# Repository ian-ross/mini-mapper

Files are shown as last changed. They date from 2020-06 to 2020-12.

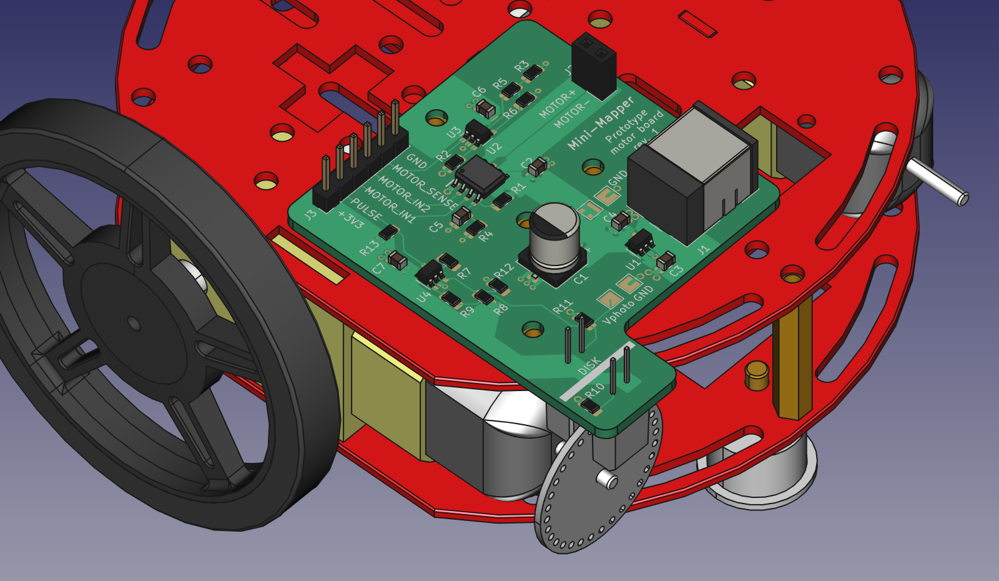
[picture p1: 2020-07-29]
prototypes/motor-board/doc/motor-prototype-setup/motor-prototype-setup.png

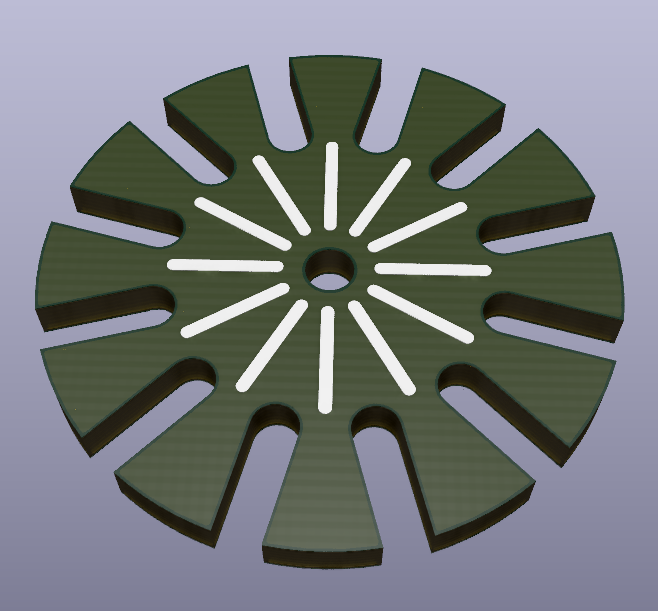
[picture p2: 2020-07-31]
prototypes/motor-board/motor-encoder-disk/v2/motor-encoder-disk.png

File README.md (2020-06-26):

# Mapping robot project experiment

Goals:

 - Learn some electronics
 - Write some interesting embedded software
 - Experiment with developing teaching materials

## Tools

 - KiCad 5.1.6

## Notes

 - All KiCad projects need to include path to top-level `lib`
   directory as a project-specific library path. This should be set up
   as a path relative to `${KIPRJMOD}`.

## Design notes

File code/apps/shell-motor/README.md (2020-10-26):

# PWM shell application

Sets up 5 kHz PWM timers on:

 * TIM10: PB8
 * TIM3: PA6, PA7, PC8, PC9

## Commands

pwm1 {on|off}
pwm4 {on|off}

## Variables

pwm1-state
pwm1-polarity
pwm1-duty
pwm1-reload

pwm4-state
pwm4-polarity-1
pwm4-polarity-2
pwm4-polarity-3
pwm4-polarity-4
pwm4-duty-1
pwm4-duty-2
pwm4-duty-3
pwm4-duty-4
pwm4-reload

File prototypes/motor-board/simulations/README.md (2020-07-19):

# Motor encoder circuit simulations

These simulations are intended to explore the threshold and hysteresis
setup for the comparator used with the photointerrupter for the motor
encoder disk.

The comparator used in the simulations is the LT1017, though that's
not what's used in the real circuit.

## Simulations

There are four different simulations here:

 * `phototransistor-saturation.asc` just demonstrates how
   phototransistors go into saturation when drive sufficiently hard,
   using a photoisolator out of the LTSpice libraries for
   experimentation.

 * `no-noise/no-noise.asc` uses a simulated current signal without any
   superimposed noise to look at how the comparator works in a simple
   case.

 * `with-noise/jitter.asc` uses a simulated current signal with some
   superimposed noise, showing the bad effects of noise leading to
   spurious comparator output transitions when the phototransistor
   current crosses the comparator threshold slowly. This is no good
   for counting pulses, so we need to add hysteresis.

 * `with-noise/hysteresis.asc` uses the same simulated current signal
   withh superimposed noise, but includes a small amount of hysteresis
   in the comparator circuit, which eliminates the spurious
   transitions in the comparator output and gives a clean pulse train
   suitable for counting the motor encoder disk holes passing the
   optical aperture of the photointerrupter.

## Phototransistor current simulations

The `scripts/gen-signal.py` script generates simulated current signals
from the phototransistor in the photointerrupter as the motor encoder
disk turns. See the `../doc/photoencoder-signal` directory for the
details of how these simulations work.

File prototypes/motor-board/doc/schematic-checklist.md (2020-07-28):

# Schematic review checklist

Is the design passively or actively safe? For example, if an MCU or
FPGA is being programmed, held in reset, or in their POR, does the
circuit enter a safe / idle / known state? Is the circuit only “hot”
under control (can it be)?

Can all relevant environmental changes be detected? If changes in
environment indicate a change in operating state or mode, can they be
detected? Examples: VBUS high on a self-powered USB device, SD card in
socket, a particular connector plugged in, water ingress, etc.

BOM has full orderable part numbers including all options and sufixes.
BOM is complete including PCB, enclosure, screws, bags, accessories,
memory cards, manuals, customer boxes, labels, master shipping carton.

## General

* [X] CAD ERC 100% clean. If some errors are invalid due to toolchain
      quirks, each exception must be inspected and signed off as invalid.
* [X] Verify pin numbers of all schematic symbols against datasheet or
      external interface specification document (if not yet board proven).
* [X] Schematic symbol matches chosen component package
* [X] Thermal pads are connected to correct power rail (may not always
      be ground)
* [?] Pull-up / -down resistors appropriate value for expected
      environment/noise?
* [X] Enable pins checked for polarity. Not all datasheets indicate
      this well, pin description text checked? Part number verified
      for ICs with orderable polarity configurations?
* [X] Enable and shutdown pins pulled to the correct level when not
      under control? (e.g. shut down unless controlled)
* [X] Pull-ups on open-drain, open-collector nets? Values for required
      slew rates / throughput / noise?
* [X] Passive / buffered visual indicators (e.g. LEDs) at appropriate
      level for the idle level of the protocol? (e.g. UART idle high,
      SPI clock idle low, etc)
* [X] Exposed pads on no-leads packages tied to correct net? Needs to
      be left floating?

## Passive components

* [X] Power/voltage/tolerance ratings specified as required
* [X] Ceramic capacitors appropriately de-rated for C/V curve
* [X] Polarized components specified in schematic if using electrolytic caps etc

## Power supply

### System power input

* [X] Check total input capacitance and add inrush limiter if needed

### Regulators

* [X] Verify estimated power usage per rail against regulator rating
* [X] Linear regulators and voltage reference ICs are stable with selected output cap ESR

### Decoupling

* [X] Decoupling present for all ICs
* [X] Decoupling meets/exceeds vendor recommendations if specified
* [X] Bulk decoupling present at PSU

### General

* [X] All power inputs fed by correct voltage
* [X] Check high-power discrete semiconductors and passives to confirm
      they can handle expected load
* [X] Analog rails filtered/isolated from digital circuitry as needed

## Signals

### Digital

* [X] Signals are correct logic level for input pin
* [X] Pullups on all open-drain outputs
* [X] Active high/low enable signal polarity correct

### Analog

* [X] Verify polarity of op-amp feedback

### Debugging / reworkability

* [X] Use 0-ohm resistors vs direct hard-wiring for strap pins when
      possible
* [X] Provide multiple ground clips/points for scope probes
* [X] Dedicated ground in close proximity to analog test points
* [X] Test points on all power rails
* [X] Test points on interesting signals which may need probing for
      bringup/debug

## Thermal

* [X] Power estimates for all large / high power ICs
* [X] Thermal calculations for all large / high power ICs
* [X] Specify heatsinks as needed

## Power

* [X] Power pins tied to correct voltage rail?
* [X] Dropout voltage of regulators checked against complete
      range/tolerance of source supply? Not just nominal/ideal rating.
* [X] Minimum load met for stability of all regulators?
* [X] Final circuit maximum load rechecked against regulator ratings?
* [X] Digital ICs have correct number and value of bypass capacitors
      for frequencies in use?
* [X] Bypass and output capacitor values checked for all regulators?
      Correctly derated? Appropriate  ESR for stability?
* [X] Analog rails properly decoupled with ferrites / inductors /
      capacitors?

## Sensors / Signal Conditioning

* [X] Dividers and filters buffered with op-amp before ADC?
* [X] Op-amp stability checked given load capacitance on output?
* [X] Unused op-amps in dual or quad packages terminated?

## Connectors

* [X] Power and its ground on same connector?
* [X] Related inputs/outputs on same connector?

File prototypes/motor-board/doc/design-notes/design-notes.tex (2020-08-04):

\documentclass[a4paper,11pt,article]{memoir}

\usepackage[utf8]{inputenc}
\usepackage{fourier}
\usepackage{amsmath,amssymb}
\usepackage{xstring,ifthen,xcolor}
\usepackage{xspace}
\usepackage{url}

\usepackage{color}
\definecolor{orange}{rgb}{0.75,0.5,0}
\definecolor{magenta}{rgb}{1,0,1}
\definecolor{cyan}{rgb}{0,1,1}
\definecolor{grey}{rgb}{0.25,0.25,0.25}
\newcommand{\outline}[1]{{\color{grey}{\scriptsize #1}}}
\newcommand{\todo}[1]{{\color{red}\textit{\textbf{#1}}}}
\newcommand{\note}[1]{{\color{blue}\textit{\textbf{#1}}}}
\newcommand{\citenote}[1]{{\color{orange}{[\textit{\textbf{#1}}]}}}

\usepackage{tikz}
\usepackage{pgfmath}
\usetikzlibrary{calc,shapes,positioning}

\title{Mini-Mapper:\,Motor prototype board design notes}
\author{Ian~Ross}

\graphicspath{{figs/}}

\begin{document}

\maketitle

These notes describe the motor prototype board for the Mini-Mapper
robot. This is intended as a platform to test motor driver and motor
encoder setup, and to develop motor early control algorithms
(particularly constant-speed PID control and soft start).

\section{Requirements}

\begin{itemize}
  \item{Power single Dagu DG01D gearmotor (4.5\,V, 250\,mA max.);}
  \item{PWM speed control, bidirectional, coast/brake functionality;}
  \item{Rotation measurement using optical encoder;}
  \item{Interface to STM32F767ZI Nucleo-144 board;}
  \item{Clean mechanical design for interface between motor and motor
    encoder disk.}
\end{itemize}

\section{Mechanical design}

\begin{itemize}
  \item{Final PCB to be mounted on top chassis plate of robot: do this
    also for prototype motor board, to get placement right.}
  \item{Principal constraints are:
    \begin{itemize}
      \item{Access to mounting holes on top chassis plate
        (there is interference with the motor under some holes);}
      \item{Clearance under PCB:\@{}both for the possibility of
        mounting components on the bottom of the PCB and for space for
        routing wires and to avoid shorts to chassis plate from THT
        components;}
      \item{Alignment of photoencoder with motor encoder disk:
        photointerrupter slot and optical axis need to align with the
        holes in the motor encoder disk, there needs to be no
        interference between the photointerrupter and the motor body,
        and there needs to be little enough interference between the
        photointerrupter and the top chassis plate to make modifying
        the chassis plate easy.}
  \end{itemize}}
  \item{Motor encoder disk needs to be manufacturable by hand, which
    means a simple disk with holes, rather than slots. This leads to a
    strong alignment requirement in the vertical direction between the
    motor encoder disk and the photointerrupter optical axis.}
\end{itemize}

\section{Component choices}

\paragraph{Motor driver: Toshiba TB67H450FNG}

Chosen to match supply voltage requirements for motors, to have a
standard PWM-capable control interface, internal current regulation
and an easy-to-use package.

\paragraph{Current sense opamp: TI TLV9051}

This is a low-side current sensing application, which imposes some
requirements on the input range of the opamp. The TLV9051 is
specifically intended for this application.

\paragraph{Photointerrupter: Vishay TCST1202}

Phototransistor type photointerrupter, because we're not going to get
a perfect transistion between full occlusion and full non-occlusion of
the photointerrupter's optical aperture, so it will be useful to be
able to set thresholds for occluded/non-occluded switching. The
primary constraints here are mechanical, since most devices like this
have similar electrical characteristics. The selected device has a
0.5\,mm wide optical aperture, which matches up with some simulations
I've done, and it can be mounted without interference with the motor
body using reasonably sized standard hardware (i.e. 5\,mm standoffs
between the PCB and the top chassis plate).

\paragraph{Motor encoder comparator: TI LMV331}

The requirements here are simple, so a jellybean comparator is a good
choice. Not an LM339 though! Something more modern. I chose a TI
LMV331, which is a single supply device available in an SOT-23 package.

\paragraph{4.5\,V regulator: TI TLV702}

Need a linear regulator to produce 4.5\,V from a 5\,V input: TI's
TLV702 is cheap, simple, can provide 300\,mA and comes in a 4.5\,V
version.

\paragraph{Power connectors}

Barrel jack from 5\,V power supply is 5.5\,mm OD with a 2\,mm pin. I
believe the positive connection is to the pin. We want to use the CUI
PJ-063AH, for which there is a footprint in the KiCad libraries.

\paragraph{Motor connectors}

2-hole 0.1'' header vertical socket (motor leads have individual 0.1''
pins).

\paragraph{Nucleo board connectors}

6-hole 0.1'' header vertical header (two digital motor control inputs,
one analogue motor coil current sense output, one digital encoder
pulse output, 3.3\,V supply, ground). I have leads with a pin on one
end and a socket on the other, so putting headers on the motor board
will allow these leads to connect from there to the sockets on the
Nucleo board.

\section{Schematic capture}

\subsection{Motor driver}

\begin{itemize}
  \item{Power decoupling: following schematic in application note.}
  \item{Current sense resistor: motors run from a 4.5\,V supply, and
    want to keep the maximum sense voltage to some small fraction of
    this. For a maximum current of 250\,mA, a sense resistor of
    400\,$\mathrm{m\Omega}$ gives a maximum sense voltage of 100\,mV.}
  \item{Current regulation: the maximum allowed motor coil current is
    set following the datasheet's instructions for setting the
    $V_\mathrm{ref}$ input.}
  \item{Current sensing: this is a simple non-inverting amplifier
    setup converting the 0--100\,mV sense voltage to a suitable range
    for input to the microcontroller's ADC (0--3\,V). Following a
    suggestion in a TI app
    note\footnote{\url{http://www.ti.com/lit/an/slva959a/slva959a.pdf}}
    about layout for motor drivers, the current sensing connections
    are highlighted to be routed as a differential pair (trying the
    net tie trick suggested in the app note to make the routing less
    confusing).}
\end{itemize}

\subsection{Motor encoder}

\begin{itemize}
  \item{The LED side of this is simple: take $V_f$ and $I_f$ from the
    datasheet and find a suitable resistor based on the power rail
    (3.3\,V, taken from the Nucleo board).}
  \item{On the phototransistor side, a current sensing resistor is
    needed. The light current from the phototransistor is quoted as
    being at least 1\,mA, and typically 2\,mA, but remember that we'll
    only be getting about half of that because of the size of the
    holes in the motor encoder disk. A $5.7\,\mathrm{k\Omega}$
    resistor will give a sense voltage of 2.85\,V for a phototransistor
    current of 0.5\,mA. Higher phototransistor currents will just lead
    to the phototransistor saturating, so the sense voltage will also
    be close to the positive rail.}
  \item{The threshold to use for the comparator used to turn the
    analogue output from the phototransistor into pulses for counting
    holes in the encoder disk is set at $V_{\mathrm{cc}} / 2$. This is
    conservative enough to be higher than any likely ``dark current'',
    which includes the true dark current from the phototransistor plus
    any additional current due to ambient light falling on the
    phototransistor.}
  \item{A bare comparator will produce spurious output transistions in
    the presence of noise (see simulations), so some hysteresis is
    included. The resistor values selected give a hysteresis of about
    0.1\,V.}
\end{itemize}

\subsection{Nucleo board interface}

Connections:
\begin{itemize}
  \item{3.3\,V power and ground;}
  \item{Two GPIO outputs for motor control (PWM-capable);}
  \item{One ADC input for motor coil current sense;}
  \item{One GPIO input for photoencoder pulses (interrupt-capable).}
\end{itemize}

Use 0.1'' headers on motor board, and connect to Nucleo board using
jumper cables, since the connections we'll want are pretty spread out.

\begin{center}
  \begin{tabular}{lcccc}
    \textbf{Use} & \textbf{PCB} & \textbf{Nucleo} & \textbf{Conn} & \textbf{Pin} \\
    Power  & \texttt{3V3} & \texttt{+3V3} & CN8 & 7\\
    Ground & \texttt{GND} & \texttt{GND} & CN8 & 11 \\
    Motor control & \texttt{IN1} & \texttt{PD14} (\texttt{TIM4\_CH3}) & CN7 & 16 \\
    Motor control & \texttt{IN2} & \texttt{PD15} (\texttt{TIM4\_CH4}) & CN7 & 18 \\
    Motor current sense & \texttt{Vsense} & \texttt{PA3} (\texttt{ADC123\_IN3}) & CN9 & 1 \\
    Encoder pulses & \texttt{PULSE} & \texttt{PG3} & CN8 & 16 \\
  \end{tabular}
\end{center}

\todo{Label connections with use and Nucleo pin names on silkscreen.}

\subsection{Power}

Supplies:
\begin{itemize}
  \item{Need 4.5\,V (250\,mA max.) for motor, and 3.3\,V for logic.}
  \item{For prototype board, use 3.3\,V supply from Nucleo board, and
    use external 5\,V wall wart supply plus linear regulator for
    4.5\,V supply.}
\end{itemize}

\subsubsection{3.3\,V}

For the 3.3\,V supply, the current draw is approximately:

\begin{center}
  \begin{tabular}{lc}
    \textbf{Component} & \textbf{Worst case current draw (mA)} \\
    Motor driver (control inputs) & 0.11 \\
    TLV9051 opamp & 0.45 \\
    LMV331 comparator & 0.1 \\
    TCST1202 photointerrupter & $25 + 2$ \\
    \textbf{Total} & \textbf{28} \\
  \end{tabular}
\end{center}

This 28\,mA total is well within the 500\,mA limit for the 3.3\,V
supply from the Nucleo board, so we can run the 3.3\,V devices on the
motor prototype board directly from the 3.3\,V supply from the Nucleo board.

\subsubsection{4.5\,V}

The current draw for the 4.5\,V supply can be up to 250\,mA from the
motor, plus perhaps 5\,mA for the motor driver. This is too much for
the 5\,V supply from the Nucleo board to supply reliably, so we need
to use a separate power source for the 4.5\,V supply.

We will use a 5\,V wall wart power supply with a TI TLV702 LDO
regulator (which comes in a 4.5\,V version and can supply 300\,mA).

\section{Layout}

\todo{Mechanical board outline: photoencoder placement, mounting
  holes. Measure carefully directly from chassis plate: just motor
  axis, mounting holes and photointerrupter location.}

\section{Assembly}

\paragraph{Mounting hardware}

5\,mm spacers between PCB and top chassis plate, M2.5 bolts and nuts
to secure PCB.

\paragraph{Power supply connections}

\end{document}

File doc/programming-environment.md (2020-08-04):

# Programming environment

Keep this as simple as possible, and keep it fun (for me, that
means Emacs, rather than an IDE). Requirements:

 * Emacs integration
 * C++
 * GCC toolchain
 * Makefiles?
 * OpenOCD + GDB
 * Minimal libraries: more or less just CMSIS register definitions to
   start with; later possibly FreeRTOS as well.

## Toolchain

### Compiler

GCC (gcc-arm-none-eabi-9-2020-q2-update)

https://developer.arm.com/-/media/Files/downloads/gnu-rm/9-2020q2/gcc-arm-none-eabi-9-2020-q2-update-x86_64-linux.tar.bz2

(Use this instead of AUR package, because it includes GDB as well.)

Install in `/big/opt/gcc-arm-none-eabi-9-2020-q2-update` and add
`/big/opt/gcc-arm-none-eabi-9-2020-q2-update/bin` to `PATH`.

### Programmer

OpenOCD

(available as an Arch package)

### Debugger

GDB

## Platform/libraries

CMSIS

## Build system

CMake

## Editor assistance

All in Emacs!

### IDE features

All this comes from `cmake-ide` + `rtags`:

 - Indexing/references
 - Code completion
 - Syntax highlighting

Need to set up some keybindings for `rtags`.

### Compile/flash/debug

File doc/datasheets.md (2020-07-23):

# Motors

 - [Dagu DG01D](http://www.dagurobot.com/DG01D-L)

# Motor drivers

### Diodes Inc.

 - [ZXBM5210](https://www.diodes.com/assets/Datasheets/ZXBM5210.pdf)

### Rohm

 - [BD60203EFV](https://fscdn.rohm.com/en/products/databook/datasheet/ic/motor/dc/bd60203efv-e.pdf)

### ST Micro

 - [STSPIN250](https://www.st.com/resource/en/datasheet/stspin250.pdf)

### TI

 - [DRV8832](https://www.ti.com/lit/ds/symlink/drv8832.pdf)
 - [DRV8833C](https://www.ti.com/lit/ds/symlink/drv8833c.pdf)
 - [DRV8833](https://www.ti.com/lit/ds/symlink/drv8833.pdf)
 - [DRV8835](https://www.ti.com/lit/ds/symlink/drv8835.pdf)
 - [DRV8836](https://www.ti.com/lit/ds/symlink/drv8836.pdf)
 - [DRV8837C](https://www.ti.com/lit/ds/symlink/drv8837c.pdf)
 - [DRV8837](https://www.ti.com/lit/ds/symlink/drv8837.pdf)
 - [DRV8838](https://www.ti.com/lit/ds/symlink/drv8838.pdf)
 - [DRV8847](https://www.ti.com/lit/ds/symlink/drv8847.pdf)
 - [DRV8848](https://www.ti.com/lit/ds/symlink/drv8848.pdf)
 - [DRV8871](https://www.ti.com/lit/ds/symlink/drv8871.pdf)

### Toshiba

 - [TB6552FTG](https://toshiba.semicon-storage.com/info/docget.jsp?did=16151&prodName=TB6552FTG)
 - [TB6559FG](https://toshiba.semicon-storage.com/info/docget.jsp?did=10158&prodName=TB6559FG)
 - [TB6641FTG](https://toshiba.semicon-storage.com/info/docget.jsp?did=11265&prodName=TB6641FTG)
 - [TB67H301FTG](https://toshiba.semicon-storage.com/info/docget.jsp?did=14095&prodName=TB67H301FTG)
 - [TB67H450FNG](https://toshiba.semicon-storage.com/info/docget.jsp?did=65346&prodName=TB67H450FNG)
 - [TC78H600FTG](https://toshiba.semicon-storage.com/info/docget.jsp?did=13606&prodName=TC78H600FTG)
 - [TC78H651AFNG](https://toshiba.semicon-storage.com/info/docget.jsp?did=64622&prodName=TC78H651AFNG)
 - TC78H660FTG

Also, [Motor Solutions Catalog](https://toshiba.semicon-storage.com/info/docget.jsp?did=11639)

# Op-amps

- [TI TLV9051](https://www.ti.com/lit/ds/symlink/tlv9052.pdf)

# Photointerrupters

 - [Vishay TCST1202](https://www.vishay.com/docs/83764/tcst1103.pdf)

# Comparators

 - [TI LMV331](https://www.ti.com/lit/ds/symlink/lmv331.pdf)

# Linear regulators

 - [TI TLV702](https://www.ti.com/lit/ds/symlink/tlv702.pdf)

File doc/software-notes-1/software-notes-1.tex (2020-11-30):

\documentclass[a4paper,11pt]{article}

\usepackage[utf8]{inputenc}
\usepackage{fourier}
\usepackage{amsmath,amssymb}
\usepackage{xstring,ifthen,xcolor}
\usepackage{xspace}
\usepackage{url}

\usepackage{color}
\definecolor{orange}{rgb}{0.75,0.5,0}
\definecolor{magenta}{rgb}{1,0,1}
\definecolor{cyan}{rgb}{0,1,1}
\definecolor{grey}{rgb}{0.25,0.25,0.25}
\newcommand{\outline}[1]{{\color{grey}{\scriptsize #1}}}
\newcommand{\todo}[1]{{\color{red}\textit{\textbf{#1}}}}
\newcommand{\note}[1]{{\color{blue}\textit{\textbf{#1}}}}
\newcommand{\citenote}[1]{{\color{orange}{[\textit{\textbf{#1}}]}}}

\usepackage{tikz}
\usepackage{pgfmath}
\usetikzlibrary{calc,shapes,positioning}

\title{Mini-Mapper Software 1:\,Motor prototype board}
\author{Ian~Ross}

\graphicspath{{figs/}}

\begin{document}

\maketitle

These notes describe software development for the motor prototype
board for the Mini-Mapper robot. This is intended as a platform to
test motor driver and motor encoder setup, and to develop motor early
control algorithms (particularly constant-speed PID control and soft
start).

I'm intending to develop all the software for the Mini-Mapper as
``bare metal'' C++. Although I'll probably end up using an RTOS later
on (almost certainly FreeRTOS), I'm going to start with a simple event
loop without an RTOS. I'll use a Nucleo board with an STM32F767ZI
microcontroller on it for development experiments, and will choose a
suitable STM32 processor to put on the final Mini-Mapper boards based
on experiences using the Nucleo board. I'm not going to use any HAL
libraries from ST Micro because I'm interested in writing device
drivers myself.

The basic requirements I want to follow are:

\begin{itemize}
  \item{\textbf{Language} Firmware written in C++, maybe doing some
    experiments with Rust later on.}
  \item{\textbf{Libraries} Use only low-level CMSIS hardware
    definitions, writing my own C++ HAL.}
  \item{\textbf{Build system} Use Make for building, possibly adding
    Meson on top of this later on.}
  \item{\textbf{IDE} Use Emacs as an IDE, setting up the necessary
    tools for comfortable development.}
  \item{\textbf{Communications} Develop a command shell to run on the
    Nucleo board, talking to a PC over a USB serial port. This will
    make it easy both to do ad hoc experiments directly talking to the
    shell with Minicom, but also to write GUI front-ends for
    experiments and data collection using Python GTK or something
    similar. (This is the approach I used for my Teensy Load project,
    and I find it really useful.)}
  \item{\textbf{STM32 features} Clocks; power; USB serial (USART + DMA
    + interrupts); GPIOs and timers for PWM motor control; ADC for
    motor coil current sensing; GPIO input, interrupt and timer for
    motor encoder pulse detection.}
\end{itemize}

I want to cover the following topics in this prototyping phase:
\begin{enumerate}
  \item{Platform setup: clocks, power, etc.}
  \item{CMSIS familiarisation.}
  \item{Blinky: platform test, clock setup, GPIO setup.}
  \item{USART setup with interrupts for RX and DMA for TX.}
  \item{USB serial command shell.}
  \item{PWM demo: more GPIO setup, timer setup, USB serial control,
    view output using AD2.}
  \item{First pass experiment GUI: commanding of motor state (on/off,
    forward/backward, PWM duty cycle), monitoring of motor coil
    current and motor encoder pulses; data saving; real-time
    graphing.}
  \item{Encapsulation of motor abstractions: \texttt{Motor::Driver}
    for PWM driver, \texttt{Motor::Torque} for motor coil current
    measurement for torque estimation, \texttt{Motor::Encoder} for the
    encoder disk measuring motor rotation and
    \texttt{Motor::Controller} for the overall control of all motor
    functions.}
  \item{Constant speed PID control, including independent optical
    speed measurement.}
  \item{Soft start/ramp control.}
\end{enumerate}

This should be enough for the first ``direct control'' milestone.

\section{Initial setup}

\subsection{Platform and tools}

\begin{itemize}
  \item{I'm using the \texttt{arm-none-eabi} version of GCC, which is
    pretty standard.}
\end{itemize}

\subsection{CMSIS}

\begin{itemize}
  \item{The only files taken from the ST Micro-supplied code are the
    header files \texttt{stm32f767xx.h}, \texttt{stm32f7xx.h} and
    \texttt{core\_cm7.h} (and some compiler support files that they
    include), the startup file \texttt{startup\_stm32f767xx.s}, the
    linker script \texttt{STM32F767ZITx\_FLASH.ld}, and
    \texttt{system\_stm32f7xx.c}, which is a small file including a
    couple of support functions to help with clock setup.}
  \item{The header files provide register-level access to all the core
    functionality of the Cortex-M7 processor (\texttt{core\_cm7.h})
    and the peripherals provided on the STM32F767ZI
    (\texttt{stm32f767xx.h} and \texttt{stm32f7xx.h}).}
  \item{The \texttt{core\_cm7.h} also provides some basic functions
    for dealing with some core processor features, like cache control,
    the interrupt controller and the SysTick timer.}
  \item{I'm basically going to use anything in these files freely, and
    I'm happy to look at examples in the STM32 HAL code to work
    through any problems I have with my own HAL code, but I'm going to
    write more or less everything starting at the bare metal ``write
    to registers'' level, since this seems like the best way to get a
    good understanding of how things really work.}
\end{itemize}

\subsection{Blinky}

\section{Software architecture}

\section{USB serial shell}

\subsection{USART setup}

\subsection{Command shell}

\section{PWM demonstration}

\section{Experiment front-end GUI}

\section{Microcontroller setup}

The Nucleo board has an STM32F767ZI processor on it.

\subsection{Motor driver}

\begin{itemize}
  \item{The Toshiba motor driver has an application note where they
    seem to suggest using $f_{\mathrm{PWM}} = 30\,\mathrm{kHz}$.}
  \item{For a 10-bit resolution PWM duty cycle, this gives a clock
    frequency of $1024 \times 30\,\mathrm{kHz} = 30.72\,\mathrm{MHz}$.}
  \item{The clock input on Nucleo board is 8\,MHz by default. To use
    this, the STM32 should be set to run on the HSE clock (High-Speed
    External) with external bypass (\texttt{RCC\_CR:HSEBYP} = 1,
    \texttt{RCC\_CR:HSEON} = 1).}
  \item{The main clock PLL should be set up with
    \texttt{RCC\_PLLCFGR:PLLSRC} = 1 (HSE), \texttt{RCC\_PLLCFGR:PLLM}
    = 4 (VCO input: 2\,MHz), \texttt{RCC\_PLLCFGR:PLLN} = 128 (VCO
    output: 256\,MHz), \texttt{RCC\_PLLCFGR:PLLP} = 4 (PLL output:
    64\,MHz), and enabled with \texttt{RCC\_CR:PLLON} = 1.}
  \item{The APB prescalers need to be set to make the low-speed
    prescaler give a frequency of less than 45\,MHz:
    \texttt{RCC\_CFGR:PPRE1} = 4 (divide by 2 to give 32\,MHz).}
  \item{The system clock needs to be set to use the PLL:
    \texttt{RCC\_CFGR:SW} = 2.}
  \item{Using a 64\,MHz system clock and a 11-bit resolution PWM duty
    cycle yields a PWM frequency of 31.25\,kHz.}
\end{itemize}

\subsection{Motor torque measurement}

\subsection{Motor encoder}

The motor encoder uses a photointerrupter and an encoder disk on the
motor shaft. The motor shaft rotation rate is reduced by a 48:1
gearbox to drive the wheels.

Here are some basic questions and notes on the software approach for
capturing the edge transitions from the encoder.

\textit{How to do edge capture? Can you do capture on multiple pins
  using the same timer? Can you do both rising and falling edges at
  the same time?}

\begin{itemize}
  \item{Timers with input capture are basically all timers except TIM6
    and TIM7 basic timers.}
  \item{Timers with multiple input capture channels are TIM9, TIM12 (2
    channels); TIM2, TIM3, TIM4, TIM5 (4 channels); TIM1, TIM8 (4
    channels).}
  \item{Typical times we'll want to measure:
    \begin{itemize}
      \item{Wheel turning at 90 rpm (max, equivalent to 28.3 cm/s
        linear speed) => encoder turning at 90 x 48 = 4320 rpm = 72
        Hz.}
      \item{Disk has 12 teeth => tooth frequency = 72 x 12 = 864 Hz.}
      \item{If teeth/gaps are same size, edge freq. = 864 x 2 = 1728
        Hz. (Teeth and gaps aren't same size, but this is
        indicative.)}
      \item{So time between edges will be 578.7 μs.}
   \end{itemize}}
  \item{If we have a timer with a prescaler set to give a count
    frequency of 1 MHz, then a 16-bit counter will be able to measure
    times of up to 65.536 ms. A 32-bit counter will be able to measure
    times of up to 4294.97 s (i.e. 1 hr 11 min 34.97 s).}
  \item{At 1 mm/s linear speed, we see 1 / (60π) * 48 * 12 * 2 = 6.11
    edges per second, i.e. an inter-edge time of 163.6 ms. Seems like
    a 32-bit timer might be easier in this case...}
  \item{If we use a 32-bit timer, we can also reduce the prescaler to
    get a higher count frequency and corresponding better timing
    accuracy.}
  \item{The 32-bit timers are TIM2 and TIM5, both of which have four
    capture channels.}
  \item{GPIO inputs for capture channels have to be assigned as
    specific alternate functions. There seem to be enough redundant
    assignments to make this easy enough to do.}
  \item{Can either get an interrupt on the capture event, or get the
    capture timer count transferred via DMA and get an interrupt on
    DMA transfer complete. (For our purposes, an interrupt on each
    capture event is probably simplest to deal with, because we need
    to look at the GPIO level to know whether we have a rising or
    falling edge. In the ISR for the capture, we can check the GPIO
    level, bundle that up with the capture count and the channel we're
    looking at, and emit an event carrying all that information for
    later processing.)}
  \item{Capture edge polarity is controlled by the CCxP and CCxNP
    fields in the TIMx->CCER register: setting both of these bits
    captures both rising and falling edges.}
\end{itemize}

\textit{What information do we want to make available? Ultimately we
  want to provide a speed measurement, possibly with different kinds
  of smoothing (none: latest instantaneous value, boxcar smoothing
  over sample time, exponentially weighted smoothing?), but we also
  probably want access to raw time values as well, i.e. times of the
  last N edge transitions.}

\begin{itemize}
  \item{For a single encoder, we expect to get a sequence of
    alternating rising and falling edges. We'll store the edge type
    (rising or falling) and the timer count when the edge occurred.
    We'll keep the last N edge times, retiring eges when they get too
    old or we need to reuse storage space.}
  \item{We want to be able to retrieve time differences between edges
    and to convert them into rotation rates and linear speeds, both on
    an instantaneous basis and smoothed over the collected data (for
    the last 500 ms or something similar?).}
  \item{To start with, let's provide functions to retrieve time
    differences between adjacent edges (i.e. of opposite polarity) and
    between adjacent edges of the same polarity.}
\end{itemize}

\textit{What sort of time resolution do we need? And what to do about
  the really slow cases when the wheel is more or less stopped? Do we
  need some sort of rollover counter to time longer periods?}

\begin{itemize}
  \item{A single edge corresponds to 60π / 48 / 12 / 2 = 0.16 mm
    (assuming symmetry of rising and falling edges).}
  \item{Using a 32-bit timer running at 1 MHz, we can get 1 μs
    resolution for each edge. At maximum speed (90 rpm for the wheel,
    i.e. 60π * 1.5 = 282.74 mm/s), 1 μs corresponds to a linear
    distance of 0.28 μm. At lower speeds, the linear distance
    resolution is correspondingly finer.}
  \item{As noted above, with a timer count frequency of 1 MHz, a
    32-bit counter is able to measure times of up to 4294.97 s (i.e. 1
    hr 11 min 34.97 s).}
  \item{Both of these factors indicate that a 1 MHz 32-bit timer is
    pretty huge overkill... So let's go with that then!}
\end{itemize}

\end{document}

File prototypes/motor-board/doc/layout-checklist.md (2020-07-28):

# Layout review checklist

## General

* [X] [Schematic review](schematic-checklist.md) complete and signed
      off, including pin swaps done during layout
* [X] DRC set up to fab constraints before layout starts?
* [X] Layout DRC 100% clean
* [X] Double check the drill vs annular ring size for vias?
* [X] Passives have Traces coming into pads symmetrically? Traces
      comming into opposing “sides” of pads can cause solder
      migration, tombstoning, or stresses when the board cools.
* [X] Margin to edge of board checked? Appropriate given board
      break-away (V-score or mouse bites)? Mouse bites can easily
      pull/crack solder mask at 20 mil in.
* [X] Components can be reworked without removing others?
* [X] Thermal reliefs for all pads of serviceable components?

## Decoupling

* [X] Decoupling caps as close to power pins as possible
* [X] Low inductance mounting used for decoupling (prefer ViP if
      available, otherwise "[]8" shaped side vias

## DFM / yield enhancement

* [X] All design rules within manufacturer's capability
* [X] Minimize use of vias/traces that push fab limits

## Footprints

* [X] Confirm components are available in the selected package
* [X] Confirm components (especially connectors and power regulators)
      are capable of desired current in the selected package
* [X] Verify schematic symbol matches the selected package
* [X] Confirm pinout diagram is from top vs bottom of package
* [X] (recommended) PCB printed 1:1 on paper and checked against
      physical parts
* [X] 3D models obtained (if available) and checked against footprints
* [X] Soldermask apertures on all SMT lands and PTH pads

## Power

* [X] Traces have sufficient width for current and allowable
      temperature rise?
* [X] Sufficient trace spacing for voltage?
* [X] Highest ground currents closest to supply return?
* [X] Via size and count appropriate for current?
* [X] Thermal vias for thermal pads?
* [X] Tenting set appropriately for thermal vias?
* [X] Thermal reliefs disabled for power component pads?
* [X] Separate supply rail traces to multiple regulators?

## Connectors

* [X] Drivers near connectors they are driving signals on?

## Mechanical

* [X] Confirm all connectors to other systems comply with the
      appropriate mechanical standard (connector orientation, key
      position, etc)
* [X] LEDs, buttons, and other UI elements on outward-facing side of
      board
* [X] Clearance around pluggable connectors for mating cable/connector
* [X] Clearance around mounting holes for screws
* [X] Confirm PCB dimensions and mounting hole size/placement against
      enclosure or card rack design
* [X] Verify mounting hole connection/isolation
* [X] Components not physically overlapping/colliding
* [X] Clearance provided around solder-in test points for probe tips
* [X] Drill holes checked? Correct hole spacing to mounting hardware?
* [X] Drill hole plating checked?
* [X] Adequate clearance around mounting holes for both the mounting
      hardware and the tool that fastens it?

## Thermal

* [X] Thermal reliefs used for plane connections (unless via is used
      for heatsinking)
* [X] Solid connections used to planes if heatsinking
* [X] Ensure thermal balance on SMT chip components to minimize risk
      of tombstoning

## Solder mask

* [X] Confirm SMD vs NSMD pad geometry
* [X] Adequate clearance around pads (typ. 50 um)
* [X] Soldermask relief set appropriately given expected soldermask
      expansion?
* [X] Soldermask minimum spoke size met?
* [X] Soldermask relief around fiducials?
* [X] Soldermask removed for all pads?

## Silkscreen

* [X] Text size within fab limits
* [X] Text not overlapping drills or component pads
* [X] Text removed entirely in, or moved outside of, high component/via density areas
* [X] Traceability markings (rev, date, name, etc) provided
* [X] Text mirrored properly on bottom layer
* [X] Test points labeled if space permits
* [X] Check fab silkscreen DPI? Can legend be printed clearly?
* [X] Pin-1 indicator visible after component is placed on board?
* [X] Power pins labeled with polarity and voltage ranges?
* [X] Connector pinouts printed on both sides of board and mirrored?
      (if two-sided silkscreen)
* [X] Part number, revision number, date code present?
* [X] Legend references all facing one or two directions?

## CAM production

* [X] KiCAD specific: rerun DRC and zone fills before exporting CAM
      files to ensure proper results
* [X] Export gerber/drill files at the same time to ensure consistency
* [X] Visually verify final CAM files to ensure no obvious
      misalignments

## Programming and Test

* [X] Test points on all important clock and data pins?
* [X] More test points?
* [X] Sure, but maybe more test points?
* [X] Ground reference test points near all high speed signals that
      might need to be probed?

## Sensing

* [X] Analog sensors close to their ADC or buffered soon?
* [X] ADCs on or toward digital part of layout? (ADCs use fast
      oscillators)
* [X] Feedback dividers accidentally bypassed with capacitor
      placement?

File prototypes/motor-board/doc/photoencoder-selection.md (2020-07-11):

# Photoencoder selection

## Type

 - Two options: phototransistor or "photo IC".
 - Phototransistor is what it says => outputs current signal depending
   on degree of occlusion of optical beam.
 - "Photo IC" is usually a photodiode, an amplifier, a Schmitt trigger
   and an output transistor => does thresholding and outputs logic
   levels. [EXAMPLE FROM TT ELECTRONICS DATASHEET]
 - Phototransistor more flexible in terms of handling partial
   occlusion/non-occlusion of optical beam; with photo IC parts, you
   need to alternate between complete occlusion and complete
   non-occlusion, I think.
 - So, use a phototransistor device.

## Electrical specifications

## Physical envelope

Need to know:

 - Length of motor output shaft (ca. 6mm) [MEASURE!!!]
 - Thickness of encoder disk material (ca. 1mm)
 - Diameter of encoder disk (22.5mm)
 - Radius of circle of centres for encoder disk holes (10mm)
 - Diameter of encoder disk holes (1mm)
 - Physical dimensions of encoders: L (along optical axis) x W
   (perpendicular to optical axos) x H (from PCB to top of encoder
   vertically), slot width (Ws) and depth (Hs), optical axis depth
   from top of encoder (Ho)

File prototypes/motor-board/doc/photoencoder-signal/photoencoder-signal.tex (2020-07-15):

\documentclass[a4paper,11pt,article]{memoir}

\usepackage[utf8]{inputenc}
\usepackage{fourier}
\usepackage{amsmath,amssymb}
\usepackage{xstring,ifthen,xcolor}
\usepackage{xspace}

\usepackage{tikz}
\usepackage{pgfmath}
\usetikzlibrary{calc,shapes,positioning}

\title{Mini-Mapper 8:\,Photoencoder signals}
\author{Ian~Ross}

\newdimen\holecircleradius{}
\pgfmathsetlength{\holecircleradius}{10mm}

\newdimen\offsetangle{}

\newcommand{\fulldisk}[1]{%
\pgfmathsetlength{\offsetangle}{#1}
\begin{tikzpicture}[scale=1.75]
  \fill[fill=red]
  (-0.25mm,\the\holecircleradius-1mm) --
  (-0.25mm,\the\holecircleradius+1mm) --
  (0.25mm,\the\holecircleradius+1mm) --
  (0.25mm,\the\holecircleradius-1mm) --
  (-0.25mm,\the\holecircleradius-1mm);

  \draw (0,0) -- (0,\the\holecircleradius+1.5mm);
  \draw (0,0) -- (90+\the\offsetangle:\the\holecircleradius+1.5mm);

  \draw[dashed] (0,0) circle [radius=\the\holecircleradius];

  \foreach \angle in {0,1,...,31}
    \draw (360/32*\angle+90+\the\offsetangle:\the\holecircleradius) circle [radius=0.5mm];
\end{tikzpicture}}

\graphicspath{{figs/}}

\begin{document}

\maketitle

\section*{Introduction}

The idea here is to calculate the form of signal that the
phototransistor in the photointerrupter on the motor encoder disk will
generate as the encoder disk rotates. This isn't strictly necessary,
but it's mildly interesting, and a fun geometrical exercise.
Figure~\ref{fig:setup} shows the basic setup, with the ring of holes
in the encoder disk rotating past the beam of the photointerrupter.

The important factor for the purposes of determining the current
signal generated by the phototransistor in the photointerrupter is the
area of overlap between the hole in the encoder disk and the beam of
infrared radiation emitted by the photodiode in the photointerrupter.

The following parameters are used in the analysis below:
\begin{itemize}
  \item{$d$: the diameter of a single hole in the encoder disk;}
  \item{$D$: the diameter of the circle of centres of the holes in the
    encoder disk;}
  \item{$w$ and $h$: the width and height of the beam from the
    photodiode in the photointerrupter --- for the photointerrupters
    I've been looking at, the beam aperture is rectangular, with the
    narrower dimension horizontal.}
  \item{$\phi$: the angle (anticlockwise positive) between the line
    between the centre of rotation of the encoder disk and the center
    of the photointerrupter beam, and the line betwen the centre of
    rotation of the encoder disk and the centre of the hole under
    consideration.}
\end{itemize}

We make a few assumptions:
\begin{enumerate}
  \item{$d \leq h$ and $d \geq w$: these assumptions give the
    geometrical relations between the optical beam and the hole as
    shown in Figure~\ref{fig:setup}, i.e., the outline of the hole has
    either zero, two or four intersections with the outline of the
    optical beam, with all intersections occurring on the vertical
    sides of the beam.}
  \item{The gaps between the holes in the encoder disk are large
    enough that only one hole can intersect with the optical beam at a
    time.}
\end{enumerate}

\begin{figure}
  \begin{center}
    \fulldisk{0}\hspace{0.5cm}\fulldisk{1}\hspace{0.5cm}\fulldisk{2}
  \end{center}

  \begin{center}
    \fulldisk{3}\hspace{0.5cm}\fulldisk{4}\hspace{0.5cm}\fulldisk{5}
  \end{center}

  \caption{Photointerrupter beam (red, $w = 0.5\,\mathrm{mm} \times h
    = 2\,\mathrm{mm}$) interfacing with holes in motor encoder disk.
    Dashed circle shows line of centres of encoder disk holes
    (diameter $D = 20\,\mathrm{mm}$), with each hole being of diameter
    $d = 1\,\mathrm{mm}$. The images here show the positions of the
    encoder disk $1^\circ$ apart, starting with a hole centrally
    located in front of the photointerrupter beam ($\phi = 0$) and
    showing positions of $\phi = 1^\circ, 2^\circ, 3^\circ, 4^\circ,
    5^\circ$.}\label{fig:setup}
\end{figure}

\section*{Intersections of holes with optical aperture}

Let's think about the overlap of a single hole with the aperture of
the photointerrupter. We'll consider only $\phi \geq 0$ (the situation
for negative $\phi$ is symmetrical). Writing $R = D / 2$ for the
radius of the circle of centres, and $r = d / 2$ for the radius of the
holes, the centre of the hole we're looking at is at $(x_c, y_c)$:
\begin{equation*}
  x_c = -R \sin \phi, \; y_c = R \cos \phi
\end{equation*}
and its equation is
\begin{equation*}
  {(x - x_c)}^2 + {(y - y_c)}^2 = r^2
\end{equation*}
or
\begin{equation*}
  {(x + R \sin \phi)}^2 + {(y - R \cos \phi)}^2 = r^2
\end{equation*}
Points of intersection of this circle with the outline of the optical
beam are given by solving this equation for $y$ when $x = \pm w/2$:
\begin{equation*}
  R^2 \sin^2 \phi \pm w R \sin \phi + w^2/4 + y^2 - 2 R y \cos \phi +
  R^2 \cos^2 \phi - r^2 = 0
\end{equation*}
or, simplifying
\begin{equation}
  \label{eq:intersection}
  y^2 - 2 R y \cos \phi + R^2 - r^2 + w^2/4 \pm w R \sin \phi = 0.
\end{equation}
This discriminant of this equation is
\begin{equation}
  \label{eq:discriminant}
  \Delta_{\pm} = 4 R^2 \cos^2 \phi \mp 4 w R \sin \phi - 4 (R^2 - r^2)
  - w^2.
\end{equation}
Figure~\ref{fig:discriminant} shows values of $\Delta_{\pm}$
from~\eqref{eq:discriminant} as a function of $\phi$. When the hole
extends right across the width of the optical beam aperture, there are
four intersections between the circle defining the outline of the hole
and the outline of the aperture. In this case, $\Delta_{+} \geq 0,
\Delta_{-} \geq 0$. When the outline of the hole intersects with only
one vertical side of the optical beam aperture, then there are two
intersections between the circle and the outline of the aperture and
$\Delta_{+} < 0, \Delta_{-} \geq 0$. When there are no intersections
between the circle and the outline of the aperture then both
discriminants are negative.

The limits in terms of the angular displacement $\phi$ of the ranges
with solutions are given by $\Delta_{\pm} = 0$.
From~\eqref{eq:discriminant}, this gives
\begin{equation*}
  4 R^2 \sin^2 \phi \pm 4 w R \sin \phi - 4 r^2 + w^2 = 0
\end{equation*}
or
\begin{align*}
  \sin \phi &= \frac{\mp 4 w R \pm \sqrt{16 w^2 R^2 - 16 R^2 (w^2 - 4 r^2)}}{8 R^2} \\
  \sin \phi &= \frac{\mp w \pm \sqrt{w^2 - (w^2 - 4 r^2)}}{2 R} \\
  \sin \phi &= \frac{\mp w \pm 2 r}{2 R}
\end{align*}

\begin{equation*}
  \sin \phi = \frac{\mp w/2 \pm r}{R}.
\end{equation*}
The four limiting values for $\phi$ derived from this equation provide
the limits of the two intersection and four intersection cases in the
positive and negative $\phi$ directions. Putting $w =
0.5\,\mathrm{mm}$, $r = 0.5\,\mathrm{mm}$ and $R = 10\,\mathrm{mm}$,
we get limits of $|\phi| \leq 4.30^\circ$ for the two intersections
case, and $|\phi| \leq 1.43^\circ$ for the four intersections case,
which matches with the limits seen in Figure~\ref{fig:discriminant}.

\begin{figure}
  \begin{center}
    
  \end{center}

  \caption{Discriminant for hole/beam intersection equation as a
    function of angular displacement $\phi$. The boundary of the ``two
    intersections'' region is $\Delta_{-}(\phi)$, while that of the
    ``four intersections'' region is $\Delta_{+}(\phi)$.}\label{fig:discriminant}
\end{figure}

Solutions to the positive and negative versions
of~\eqref{eq:intersection} exist when $\Delta_{\pm} \geq 0$ and are
given by:
\begin{equation}
  \label{eq:solutions}
  y_{\color{black}\pm}^{\color{red}\pm} = R \cos \phi {\color{red}\pm} \frac12
  \sqrt{\Delta_{\pm}} = y_c {\color{red}\pm} \frac12
  \sqrt{\Delta_{\pm}}
\end{equation}
(The sign of the discriminant $\Delta_{\pm}$ matches the sign on the
left hand side. The other plus-or-minus sign is for the usual pair of
solutions to a quadratic equation, and corresponds to the two members
of the pairs of intersection points.) Figure~\ref{fig:solutions} shows
these solutions as a function of $\phi$.

\begin{figure}
  \begin{center}
    
  \end{center}

  \caption{Solutions for hole/beam intersection equation as a function
    of angular displacement $\phi$. The $y_{-}$ values show
    intersections with the left-hand edge of the optical aperture
    (remember positive $\phi$ means movement of the hole to the left
    from top dead centre), and $y_{+}$ values are for intersection
    with the right-hand edge of the aperture. The ``(pos)'' and
    ``(neg)'' labels indicate the two signs in~\eqref{eq:solutions}
    for the two solutions to each quadratic
    equation.}\label{fig:solutions}
\end{figure}

\section*{Hole/aperture overlap area}

Given the intersection information from~\eqref{eq:solutions}, we now
need to calculate the area of the overlap between the encoder disk
hole and the photointerrupter optical aperture. There are three cases
to consider, two requiring calculation and one trivial:
\begin{enumerate}
  \item{There are two intersections between the outline of the hole
    and the optical aperture. In this case, the overlap between the
    hole and aperture is formed by a line segment of the vertical side
    of the aperture and a segment of the circle forming the outline of
    the hole --- this segment lies inside the optical aperture and has
    endpoints given by the intersection points between the hole and
    the vertical side of the aperture (Figure~\ref{fig:overlaps}a).}
  \item{There are four intersections between the outline of the hole
    and the optical aperture. In this case, the overlap is the encoder
    disk hole minus two segments of the circle forming the outline of
    the hole --- these segments lie outside the optical aperture and
    have endpoints given by the intersection points between the hole
    and the vertical sides of the aperture
    (Figure~\ref{fig:overlaps}b).}
  \item{There are no intersections between the outline of the encoder
    disk hole and the optical aperture. In this trivial case, the
    overlap area is identically zero.}
\end{enumerate}
In each of the two cases requiring calculation, the calculation can be
performed on the basis of an expression for the area of a segment of a
circle. For a circle with radius $R$, the area $A$ of a segment
subtending an angle $\theta$ at the centre of the circle is
\begin{equation}
  \label{eq:segment}
  A = \frac{R^2}{2} (\theta - \sin \theta).
\end{equation}

\begin{figure}
  \begin{center}
    \begin{tabular}{cc}
     &
     \\
    (a) Two intersections & (b) Four intersections
    \end{tabular}
  \end{center}

  \caption{Overlap cases: (a) two intersections, so overlap is a
    segment of a circle; (b) four intersections, so overlap is a
    circle minus two segments.}\label{fig:overlaps}
\end{figure}

\subsection*{Case 1: two intersections}

Figure~\ref{fig:overlaps}a shows this case. The intersection points of
the outline of the encoder disk hole and the optical aperture are
$(-w/2, y_{-}^{+})$ and $(-w/2, y_{-}^{-})$. We know the radius of the
encoder disk hole, so in order to apply~\eqref{eq:segment} to
calculate the area of overlap, we need to find the angle $\theta$. To
do this, we construct vectors $\mathbf{v}_{+}$ and $\mathbf{v}_{-}$
between the centre of the encoder disk hole and the intersection
points:
\begin{equation}
  \mathbf{v}_{+} = \begin{pmatrix}
    -w/2 - x_c \\
    y_{-}^{+} - y_c
  \end{pmatrix}, \;\;\;\;\;\;
  \mathbf{v}_{-} = \begin{pmatrix}
    -w/2 - x_c \\
    y_{-}^{-} - y_c
  \end{pmatrix},
\end{equation}
and then
\begin{equation*}
  \cos \theta = \hat{\mathbf{v}}_{+} \cdot \hat{\mathbf{v}}_{-}.
\end{equation*}
(Here $\hat{\mathbf{v}}$ is the unit vector in the direction of vector
$\mathbf{v}$.) First we calculate $\mathbf{v}_{+} \cdot
\mathbf{v}_{-}$, making use of the fact that $y_{-}^{\pm} - y_c = \pm
\frac12 \sqrt{\Delta_{-}}$ (from~\eqref{eq:solutions}):
\begin{equation}
  \mathbf{v}_{+} \cdot \mathbf{v}_{-} = {\left(\frac{w}{2} +
    x_c\right)}^2 + (y_{-}^{+} - y_c) (y_{-}^{-} - y_c) =
         {\left(\frac{w}{2} + x_c\right)}^2 - \frac{\Delta_{-}}{4}.
\end{equation}
Now, we also find that
\begin{align*}
  |\mathbf{v}_{\pm}|^2 = {\left(\frac{w}{2} + x_c\right)}^2 + {(y_{-}^{\pm} -
  y_c)}^2 = {\left(\frac{w}{2} + x_c\right)}^2 + \frac{\Delta_{-}}{4}.
\end{align*}
so that
\begin{equation*}
  |\mathbf{v}_{+}| |\mathbf{v}_{+}| = {\left(\frac{w}{2} +
    x_c\right)}^2 + \frac{\Delta_{-}}{4}
\end{equation*}
and we finally arrive at
\begin{equation*}
  \cos \theta = \frac{\mathbf{v}_{+} \cdot
    \mathbf{v}_{-}}{|\mathbf{v}_{+}| |\mathbf{v}_{+}|} =
  \frac{{\left(\frac{w}{2} + x_c\right)}^2 -
    \frac{\Delta_{-}}{4}}{{\left(\frac{w}{2} + x_c\right)}^2 +
    \frac{\Delta_{-}}{4}}
\end{equation*}
which gives an area for the two intersection case of
\begin{equation*}
  A_2 = \frac{r^2}{2} (\theta - \sin \theta)
\end{equation*}

\subsection*{Case 2: four intersections}

The four intersections case (Figure~\ref{fig:overlaps}b) is similar,
except that we have two angles, $\theta_{-}$ and $\theta_{-}$, one of
each side of the optical aperture, and the area of interest is the
total area of the encoder disk hole minus the area of the two segments
subtended by $\theta_{-}$ and $\theta_{-}$.

The left-hand side of Figure~\ref{fig:overlaps}b can be treated the
same way as for the two intersections case:
\begin{equation}
  \cos \theta_{-} = \frac{\mathbf{w}_{+} \cdot
    \mathbf{w}_{-}}{|\mathbf{w}_{+}| |\mathbf{w}_{+}|} =
  \frac{{\left(\frac{w}{2} + x_c\right)}^2 -
    \frac{\Delta_{-}}{4}}{{\left(\frac{w}{2} + x_c\right)}^2 +
    \frac{\Delta_{-}}{4}}.
\end{equation}
The right-hand side goes the same kind of way, with vectors
$\mathbf{v}_{+}$ and $\mathbf{v}_{-}$ defined as:
\begin{equation}
  \mathbf{v}_{+} = \begin{pmatrix}
    w/2 - x_c \\
    y_{+}^{+} - y_c
  \end{pmatrix}, \;\;\;\;\;\;
  \mathbf{v}_{-} = \begin{pmatrix}
    w/2 - x_c \\
    y_{+}^{-} - y_c
  \end{pmatrix},
\end{equation}
so that
\begin{equation}
  \mathbf{v}_{+} \cdot \mathbf{v}_{-} = {\left(\frac{w}{2} -
    x_c\right)}^2 + (y_{+}^{+} - y_c) (y_{+}^{-} - y_c) =
         {\left(\frac{w}{2} - x_c\right)}^2 - \frac{\Delta_{+}}{4}.
\end{equation}
and
\begin{align*}
  |\mathbf{v}_{\pm}|^2 = {\left(\frac{w}{2} - x_c\right)}^2 + {(y_{+}^{\pm} -
  y_c)}^2 = {\left(\frac{w}{2} - x_c\right)}^2 + \frac{\Delta_{+}}{4}.
\end{align*}
so that
\begin{equation*}
  |\mathbf{v}_{+}| |\mathbf{v}_{+}| = {\left(\frac{w}{2} -
    x_c\right)}^2 + \frac{\Delta_{+}}{4}
\end{equation*}
and we arrive at
\begin{equation*}
  \cos \theta_{+} = \frac{\mathbf{v}_{+} \cdot
    \mathbf{v}_{-}}{|\mathbf{v}_{+}| |\mathbf{v}_{+}|} =
  \frac{{\left(\frac{w}{2} - x_c\right)}^2 -
    \frac{\Delta_{+}}{4}}{{\left(\frac{w}{2} - x_c\right)}^2 +
    \frac{\Delta_{+}}{4}}.
\end{equation*}
The total area in the four intersections case is then:
\begin{equation*}
  A_4 = \pi r^2 - \frac{r^2}{2} (\theta_{+} - \sin \theta_{+}) -
  \frac{r^2}{2} (\theta_{-} - \sin \theta_{-}).
\end{equation*}

\section*{Final results}

The functional dependence of the overlap area between an encoder disk
hole and the optical beam of the interrupter is shown in
Figure~\ref{fig:overlap-areas}, representing the overlap as the
fraction of the photointerrupter optical beam covered by the encoder
hole disk. The assumption is that the current generated by the
phototransistor in the photointerrupter will be proportional to this
fractional overlap.

We can now use these results to generate simulated photocurrent
signals for use in simulations.

\begin{figure}
  \begin{center}
    
  \end{center}

  \caption{Dependence of fraction of area of photointerrupter optical
    beam covered by encoder disk hole as a function of angular
    displacement $\phi$, based on $w = 0.5\,\mathrm{mm}$, $r =
    0.5\,\mathrm{mm}$ and $R = 10\,\mathrm{mm}$.}\label{fig:overlap-areas}
\end{figure}

\section*{Generation of simulated signals}

Based on the results so far, we want to be able to generate PWL
(piecewise linear) data files for use in LTSpice simulations. We'll do
this with a Python script. Basically, the script just duplicates the
calculations performed above, and produces a time series of simulated
phototransistor current values, based on a time profile of wheel
velocity. We assume that the phototransistor current is proportional
to the fraction of the optical aperture that is overlapped by the
motor encoder disk hole.

The calculations go something like this, stepping the simulation time
by a constant timestep (I've been using $\Delta t = 0.1\,\mathrm{ms}$):
\begin{enumerate}
  \item{Determine the current linear velocity from the current
    simulation time. The example I've been using starts from rest,
    accelerates to a constant speed, has a constant velocity segment,
    then decelerates back to rest. Acceleration and deceleration are
    both eased using a parabolic easing function.}
  \item{Step the current distance, wheel angle and encoder disk angle
    using simple Euler integration.}
  \item{Normalise the encoder disk angle into the range $|\phi| \leq
    \Delta \phi / 2$, where $\Delta \phi$ is the angular separation
    between adjacent holes in the encoder disk.}
  \item{We can then apply the calculations in the first part of this
    document to the angle $\phi$ to get the area overlap fraction
    between the optical aperture and the hole in the encoder disk.}
  \item{Multiply the area overlap fraction by the maximum light
    current generated by the phototransistor (I'm using
    $I_L(\mathrm{max}) = 2\,\mathrm{mA}$, which is based on the
    ``typical'' value for the Vishay TCST1230 photointerrupter I'm
    planning to use.)}
\end{enumerate}
The results of this procedure are shown in
Figure~\ref{fig:simulation}.

\begin{figure}
  \begin{center}
    
  \end{center}
  \begin{center}
    
  \end{center}
  \begin{center}
    
  \end{center}
  \begin{center}
    
  \end{center}

  \caption{Simulated phototransistor current based on using a Vishay
    TCST1230 photointerrupter, an encoder disk with 32 holes of 1\,mm
    diameter on a 20\,mm diameter circle, and a linear velocity
    profile starting from rest, increasing to 50\,mm/s in 3 seconds,
    travelling at constant speed for 2 seconds, then decelerating back
    to rest in 3 seconds.}\label{fig:simulation}
\end{figure}

\end{document}

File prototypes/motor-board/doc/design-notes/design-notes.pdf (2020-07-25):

## Mini-Mapper: Motor prototype board design notes

Ian Ross

July 25, 2020

These notes describe the motor prototype board for the Mini-Mapper robot. This is intended as a platform to test motor driver and motor encoder setup, and to develop motor early control algorithms (particularly constant-speed PID control and soft start).

## Requirements

- Power single Dagu DG01D gearmotor (4.5 V, 250 mA max.);
- PWM speed control, bidirectional, coast/brake functionality;
- Rotation measurement using optical encoder;
- Interface to STM32F767ZI Nucleo-144 board;
- Clean mechanical design for interface between motor and motor encoder disk.

## Mechanical design

- Final PCB to be mounted on top chassis plate of robot: do this also for prototype motor board, to get placement right.
- Principal constraints are:

– Access to mounting holes on top chassis plate (there is interference with the motor under some holes);

– Clearance under PCB:both for the possibility of mounting components on the bottom of the PCB and for space for routing wires and to avoid shorts to chassis plate from THT components;

– Alignment of photoencoder with motor encoder disk: photointerrupter slot and optical axis need to align with the holes in the motor encoder disk, there needs to be no interference between the photointerrupter and the motor body, and there needs to be little enough interference between the photointerrupter and the top chassis plate to make modifying the chassis plate easy.

1

- Motor encoder disk needs to be manufacturable by hand, which means a simple disk with holes, rather than slots. This leads to a strong alignment requirement in the vertical direction between the motor encoder disk and the photointerrupter optical axis.

## Component choices

Motor driver: Toshiba TB67H450FNG Chosen to match supply voltage requirements for motors, to have a standard PWM-capable control interface, internal current regulation and an easy-to-use package.

Current sense opamp: TI TLV9051 This is a low-side current sensing application, which imposes some requirements on the input range of the opamp. The TLV9051 is specifically intended for this application.

Photointerrupter: Vishay TCST1202 Phototransistor type photointerrupter, because we’re not going to get a perfect transistion between full occlusion and full non-occlusion of the photointerrupter’s optical aperture, so it will be useful to be able to set thresholds for occluded/non-occluded switching. The primary constraints here are mechanical, since most devices like this have similar electrical characteristics. The selected device has a 0.5 mm wide optical aperture, which matches up with some simulations I’ve done, and it can be mounted without interference with the motor body using reasonably sized standard hardware (i.e. 5 mm standoffs between the PCB and the top chassis plate).

Motor encoder comparator: TI LMV331 The requirements here are simple, so a jellybean comparator is a good choice. Not an LM339 though! Something more modern. I chose a TI LMV331, which is a single supply device available in an SOT-23 package.

### 4.5 V regulator: TI TLV702 Need a linear regulator to produce 4.5 V from a 5 V

input: TI’s TLV702 is cheap, simple, can provide 300 mA and comes in a 4.5 V version.

Power connectors Barrel jack from 5 V power supply is 5.5 mm OD with a 2 mm pin. I believe the positive connection is to the pin. We want to use the CUI PJ-063AH, for which there is a footprint in the KiCad libraries.

Motor connectors 2-hole 0.1” header vertical socket (motor leads have individual 0.1” pins).

2

Nucleo board connectors 6-hole 0.1” header vertical header (two digital motor control inputs, one analogue motor coil current sense output, one digital encoder pulse output, 3.3 V supply, ground). I have leads with a pin on one end and a socket on the other, so putting headers on the motor board will allow these leads to connect from there to the sockets on the Nucleo board.

## Schematic capture

Motor driver

- Power decoupling: following schematic in application note.
- Current sense resistor: motors run from a 4.5 V supply, and want to keep the maximum sense voltage to some small fraction of this. For a maximum current of 250 mA, a sense resistor of 400 mΩ gives a maximum sense voltage of 100 mV.
- Current regulation: the maximum allowed motor coil current is set following the datasheet’s instructions for setting the Vref input.
- Current sensing: this is a simple non-inverting amplifier setup converting the 0–100 mV sense voltage to a suitable range for input to the microcontroller’s ADC (0–3 V). Following a suggestion in a TI app note¹
about layout for motor drivers, the current sensing connections are highlighted to be routed as a differential pair (trying the net tie trick suggested in the app note to make the routing less confusing).

Motor encoder

- The LED side of this is simple: take Vf and If
from the datasheet and find a suitable resistor based on the power rail (3.3 V, taken from the Nucleo board).
- On the phototransistor side, a current sensing resistor is needed. The light current from the phototransistor is quoted as being at least 1 mA, and typically 2 mA, but remember that we’ll only be getting about half of that because of the size of the holes in the motor encoder disk. A 5.7 kΩ resistor will give a sense voltage of 2.85 V for a phototransistor current of 0.5 mA. Higher phototransistor currents will just lead to the phototransistor saturating, so the sense voltage will also be close to the positive rail.
- The threshold to use for the comparator used to turn the analogue output from the phototransistor into pulses for counting holes in the encoder disk is set at Vcc/2. This is conservative enough to be higher than any likely “dark current”, which includes the true dark current from the phototransistor plus any additional current due to ambient light falling on the phototransistor.

1http://www.ti.com/lit/an/slva959a/slva959a.pdf

3

- A bare comparator will produce spurious output transistions in the presence of noise (see simulations), so some hysteresis is included. The resistor values selected give a hysteresis of about 0.1 V.

Nucleo board interface

Connections:

- 3.3 V power and ground;
- Two GPIO outputs for motor control (PWM-capable);
- One ADC input for motor coil current sense;
- One GPIO input for photoencoder pulses (interrupt-capable).

Use 0.1” headers on motor board, and connect to Nucleo board using jumper cables, since the connections we’ll want are pretty spread out.

Use | PCB | Nucleo | Conn | Pin
Power | 3V3 | +3V3 | CN8 | 7
Ground | GND | GND | CN8 | 11
Motor control | IN1 | PD14 (TIM4_CH3) | CN7 | 16
Motor control | IN2 | PD15 (TIM4_CH4) | CN7 | 18
Motor current sense | Vsense | PA3 (ADC123_IN3) | CN9 | 1
Encoder pulses | PULSE | PG3 | CN8 | 16

Label connections with use and Nucleo pin names on silkscreen.

Power

Supplies:

- Need 4.5 V (250 mA max.) for motor, and 3.3 V for logic.
- For prototype board, use 3.3 V supply from Nucleo board, and use external 5 V wall wart supply plus linear regulator for 4.5 V supply.

### 3.3 V

For the 3.3 V supply, the current draw is approximately:

Component | Worst case current draw (mA)
Motor driver (control inputs) | 0.11
TLV9051 opamp | | 0.45
LMV331 comparator | | 0.1
TCST1202 photointerrupter | 25+2
Total | | 28
| | 4

This 28 mA total is well within the 500 mA limit for the 3.3 V supply from the Nucleo board, so we can run the 3.3 V devices on the motor prototype board directly from the 3.3 V supply from the Nucleo board.

### 4.5 V

The current draw for the 4.5 V supply can be up to 250 mA from the motor, plus perhaps 5 mA for the motor driver. This is too much for the 5 V supply from the Nucleo board to supply reliably, so we need to use a separate power source for the 4.5 V supply.
We will use a 5 V wall wart power supply with a TI TLV702 LDO regulator (which comes in a 4.5 V version and can supply 300 mA).

## Layout

Mechanical board outline: photoencoder placement, mounting holes. Measure carefully directly from chassis plate: just motor axis, mounting holes and photointerrupter location.

## Assembly

Mounting hardware 5 mm spacers between PCB and top chassis plate, M2.5 bolts and nuts to secure PCB.

Power supply connections

## Software

Motor driver

- The Toshiba motor driver has an application note where they seem to suggest using fPWM = 30 kHz.
- For a 10-bit resolution PWM duty cycle, this gives a clock frequency of 1024× 30 kHz = 30.72MHz.
- The clock input on Nucleo board is 8 MHz by default. To use this, the STM32 should be set to run on the HSE clock (High-Speed External) with external bypass (RCC_CR:HSEBYP = 1, RCC_CR:HSEON = 1).
- The main clock PLL should be set up with RCC_PLLCFGR:PLLSRC = 1 (HSE), RCC_PLLCFGR:PLLM = 4 (VCO input: 2 MHz), RCC_PLLCFGR:PLLN = 128 (VCO output: 256 MHz), RCC_PLLCFGR:PLLP = 4 (PLL output: 64 MHz), and enabled with RCC_CR:PLLON = 1.

5

- The APB prescalers need to be set to make the low-speed prescaler give a frequency of less than 45 MHz: RCC_CFGR:PPRE1 = 4 (divide by 2 to give 32 MHz).
- The system clock needs to be set to use the PLL: RCC_CFGR:SW = 2.

6

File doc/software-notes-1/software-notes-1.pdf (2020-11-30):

## Mini-Mapper Software 1: Motor prototype board

Ian Ross

November 30, 2020

These notes describe software development for the motor prototype board for the Mini-Mapper robot. This is intended as a platform to test motor driver and motor encoder setup, and to develop motor early control algorithms (particularly constant-speed PID control and soft start).
I’m intending to develop all the software for the Mini-Mapper as “bare metal” C++. Although I’ll probably end up using an RTOS later on (almost certainly FreeRTOS), I’m going to start with a simple event loop without an RTOS. I’ll use a Nucleo board with an STM32F767ZI microcontroller on it for development experiments, and will choose a suitable STM32 processor to put on the final Mini-Mapper boards based on experiences using the Nucleo board. I’m not going to use any HAL libraries from ST Micro because I’m interested in writing device drivers myself.
The basic requirements I want to follow are:
- Language Firmware written in C++, maybe doing some experiments with Rust later on.
- Libraries Use only low-level CMSIS hardware definitions, writing my own C++ HAL.
- Build system Use Make for building, possibly adding Meson on top of this later on.
- IDE Use Emacs as an IDE, setting up the necessary tools for comfortable development.
- Communications Develop a command shell to run on the Nucleo board, talking to a PC over a USB serial port. This will make it easy both to do ad hoc experiments directly talking to the shell with Minicom, but also to write GUI front-ends for experiments and data collection using Python GTK or something similar. (This is the approach I used for my Teensy Load project, and I find it really useful.)
- STM32 features Clocks; power; USB serial (USART + DMA + interrupts); GPIOs and timers for PWM motor control; ADC for motor coil current sensing; GPIO input, interrupt and timer for motor encoder pulse detection.

1

I want to cover the following topics in this prototyping phase:

1. Platform setup: clocks, power, etc.
2. CMSIS familiarisation.
3. Blinky: platform test, clock setup, GPIO setup.
4. USART setup with interrupts for RX and DMA for TX.
5. USB serial command shell.
6. PWM demo: more GPIO setup, timer setup, USB serial control, view output using AD2.
7. First pass experiment GUI: commanding of motor state (on/off, forward/backward, PWM duty cycle), monitoring of motor coil current and motor encoder
pulses; data saving; real-time graphing.
8. Encapsulation of motor abstractions: Motor::Driver for PWM driver, Motor::Torque for motor coil current measurement for torque estimation, Motor::Encoder
for the encoder disk measuring motor rotation and Motor::Controller
for the overall control of all motor functions.
9. Constant speed PID control, including independent optical speed measurement.
10. Soft start/ramp control.

This should be enough for the first “direct control” milestone.

## 1 Initial setup

### 1.1 Platform and tools

- I’m using the arm-none-eabi version of GCC, which is pretty standard.

### 1.2 CMSIS

- The only files taken from the ST Micro-supplied code are the header files stm32f767xx.h, stm32f7xx.h and core_cm7.h (and some compiler support files that they include), the startup file startup_stm32f767xx.s, the linker script STM32F767ZITx_FLASH.ld, and system_stm32f7xx.c, which is a small file including a couple of support functions to help with clock setup.
- The header files provide register-level access to all the core functionality of the Cortex-M7 processor (core_cm7.h) and the peripherals provided on the STM32F767ZI (stm32f767xx.h and stm32f7xx.h).

2

- The core_cm7.h also provides some basic functions for dealing with some core processor features, like cache control, the interrupt controller and the SysTick timer.
- I’m basically going to use anything in these files freely, and I’m happy to look at examples in the STM32 HAL code to work through any problems I have with my own HAL code, but I’m going to write more or less everything starting at the bare metal “write to registers” level, since this seems like the best way to get a good understanding of how things really work.

### 1.3 Blinky

## 2 Software architecture

## 3 USB serial shell

### 3.1 USART setup

### 3.2 Command shell

## 4 PWM demonstration

## 5 Experiment front-end GUI

## 6 Microcontroller setup

The Nucleo board has an STM32F767ZI processor on it.

### 6.1 Motor driver

- The Toshiba motor driver has an application note where they seem to suggest using fPWM = 30 kHz.
- For a 10-bit resolution PWM duty cycle, this gives a clock frequency of 1024×30 kHz = 30.72MHz.
- The clock input on Nucleo board is 8 MHz by default. To use this, the STM32 should be set to run on the HSE clock (High-Speed External) with external bypass (RCC_CR:HSEBYP = 1, RCC_CR:HSEON = 1).
- The main clock PLL should be set up with RCC_PLLCFGR:PLLSRC = 1 (HSE), RCC_PLLCFGR:PLLM = 4 (VCO input: 2 MHz), RCC_PLLCFGR:PLLN = 128 (VCO output: 256 MHz), RCC_PLLCFGR:PLLP = 4 (PLL output: 64 MHz), and enabled with RCC_CR:PLLON = 1.

3

- The APB prescalers need to be set to make the low-speed prescaler give a frequency of less than 45 MHz: RCC_CFGR:PPRE1 = 4 (divide by 2 to give 32 MHz).
- The system clock needs to be set to use the PLL: RCC_CFGR:SW = 2.
- Using a 64 MHz system clock and a 11-bit resolution PWM duty cycle yields a PWM frequency of 31.25 kHz.

### 6.2 Motor torque measurement

### 6.3 Motor encoder

The motor encoder uses a photointerrupter and an encoder disk on the motor shaft. The motor shaft rotation rate is reduced by a 48:1 gearbox to drive the wheels.
Here are some basic questions and notes on the software approach for capturing the edge transitions from the encoder.
How to do edge capture? Can you do capture on multiple pins using the same timer? Can you do both rising and falling edges at the same time?
- Timers with input capture are basically all timers except TIM6 and TIM7 basic timers.
- Timers with multiple input capture channels are TIM9, TIM12 (2 channels); TIM2, TIM3, TIM4, TIM5 (4 channels); TIM1, TIM8 (4 channels).
- Typical times we’ll want to measure:

– Wheel turning at 90 rpm (max, equivalent to 28.3 cm/s linear speed) => encoder turning at 90 x 48 = 4320 rpm = 72 Hz.

– Disk has 12 teeth => tooth frequency = 72 x 12 = 864 Hz.

– If teeth/gaps are same size, edge freq. = 864 x 2 = 1728 Hz. (Teeth and gaps aren’t same size, but this is indicative.)

– So time between edges will be 578.7 s.

- If we have a timer with a prescaler set to give a count frequency of 1 MHz, then a 16-bit counter will be able to measure times of up to 65.536 ms. A 32-bit counter will be able to measure times of up to 4294.97 s (i.e. 1 hr 11 min 34.97 s).
- At 1 mm/s linear speed, we see 1 / (60) * 48 * 12 * 2 = 6.11 edges per second, i.e. an inter-edge time of 163.6 ms. Seems like a 32-bit timer might be easier in this case...
- If we use a 32-bit timer, we can also reduce the prescaler to get a higher count frequency and corresponding better timing accuracy.

4

- The 32-bit timers are TIM2 and TIM5, both of which have four capture channels.
- GPIO inputs for capture channels have to be assigned as specific alternate functions. There seem to be enough redundant assignments to make this easy enough to do.
- Can either get an interrupt on the capture event, or get the capture timer count transferred via DMA and get an interrupt on DMA transfer complete. (For our purposes, an interrupt on each capture event is probably simplest to deal with, because we need to look at the GPIO level to know whether we have a rising or falling edge. In the ISR for the capture, we can check the GPIO level, bundle that up with the capture count and the channel we’re looking at, and emit an event carrying all that information for later processing.)
- Capture edge polarity is controlled by the CCxP and CCxNP fields in the TIMx->CCER register: setting both of these bits captures both rising and falling edges.

What information do we want to make available? Ultimately we want to provide a speed measurement, possibly with different kinds of smoothing (none: latest instantaneous value, boxcar smoothing over sample time, exponentially weighted smoothing?), but we also probably want access to raw time values as well, i.e. times of the last N edge transitions.

- For a single encoder, we expect to get a sequence of alternating rising and falling edges. We’ll store the edge type (rising or falling) and the timer count when the edge occurred. We’ll keep the last N edge times, retiring eges when they get too old or we need to reuse storage space.
- We want to be able to retrieve time differences between edges and to convert them into rotation rates and linear speeds, both on an instantaneous basis and smoothed over the collected data (for the last 500 ms or something similar?).
- To start with, let’s provide functions to retrieve time differences between adjacent edges (i.e. of opposite polarity) and between adjacent edges of the same polarity.

What sort of time resolution do we need? And what to do about the really slow cases when the wheel is more or less stopped? Do we need some sort of rollover counter to time longer periods?

- A single edge corresponds to 60 / 48 / 12 / 2 = 0.16 mm (assuming symmetry of rising and falling edges).

5

- Using a 32-bit timer running at 1 MHz, we can get 1 s resolution for each edge. At maximum speed (90 rpm for the wheel, i.e. 60 * 1.5 = 282.74 mm/s), 1 s corresponds to a linear distance of 0.28 m. At lower speeds, the linear distance resolution is correspondingly finer.
- As noted above, with a timer count frequency of 1 MHz, a 32-bit counter is able to measure times of up to 4294.97 s (i.e. 1 hr 11 min 34.97 s).
- Both of these factors indicate that a 1 MHz 32-bit timer is pretty huge overkill... So let’s go with that then!

6

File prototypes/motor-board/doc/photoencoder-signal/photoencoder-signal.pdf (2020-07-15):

## Mini-Mapper 8: Photoencoder signals

Ian Ross

July 14, 2020

## Introduction

The idea here is to calculate the form of signal that the phototransistor in the photointerrupter on the motor encoder disk will generate as the encoder disk rotates. This isn’t strictly necessary, but it’s mildly interesting, and a fun geometrical exercise. Figure 1 shows the basic setup, with the ring of holes in the encoder disk rotating past the beam of the photointerrupter.
The important factor for the purposes of determining the current signal generated by the phototransistor in the photointerrupter is the area of overlap between the hole in the encoder disk and the beam of infrared radiation emitted by the photodiode in the photointerrupter.
The following parameters are used in the analysis below:
- d: the diameter of a single hole in the encoder disk;
- D: the diameter of the circle of centres of the holes in the encoder disk;
- w and h: the width and height of the beam from the photodiode in the photointerrupter — for the photointerrupters I’ve been looking at, the beam aperture is rectangular, with the narrower dimension horizontal.
- φ: the angle (anticlockwise positive) between the line between the centre of rotation of the encoder disk and the center of the photointerrupter beam, and the line betwen the centre of rotation of the encoder disk and the centre of the hole under consideration.

We make a few assumptions:

1. d ≤ h and d ≥ w: these assumptions give the geometrical relations between the optical beam and the hole as shown in Figure 1, i.e., the outline of the hole has either zero, two or four intersections with the outline of the optical beam, with all intersections occurring on the vertical sides of the beam.
2. The gaps between the holes in the encoder disk are large enough that only one hole can intersect with the optical beam at a time.

1

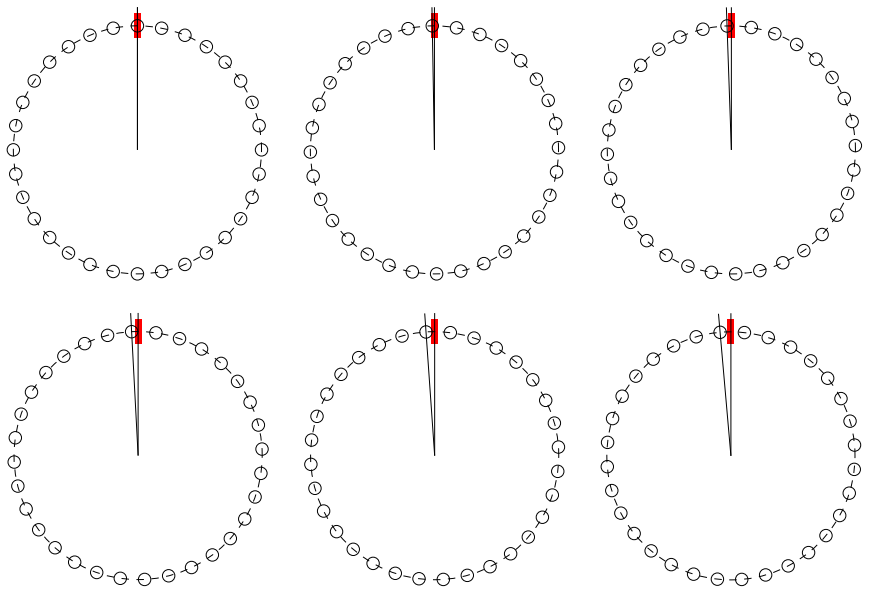
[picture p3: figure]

Figure 1: Photointerrupter beam (red, w = 0.5mm × h = 2mm) interfacing with holes in motor encoder disk. Dashed circle shows line of centres of encoder disk holes (diameter D = 20mm), with each hole being of diameter d = 1mm. The images here show the positions of the encoder disk 1◦
apart, starting with a hole centrally located in front of the photointerrupter beam (φ = 0) and showing positions of φ = 1

◦

, 2◦

, 3◦

, 4◦

, 5◦

## Intersections of holes with optical aperture

Let’s think about the overlap of a single hole with the aperture of the photointerrupter. We’ll consider only φ ≥ 0 (the situation for negative φ is symmetrical). Writing R = D/2 for the radius of the circle of centres, and r = d/2 for the radius of the holes, the centre of the hole we’re looking at is at (xc , yc ):

xc = −R sinφ, yc = R cosφ

and its equation is
(x − xc )

2 +(y − yc )

2 = r

2

or
(x +R sinφ)

2 +(y −R cosφ)

2 = r

2

Points of intersection of this circle with the outline of the optical beam are given by solving this equation for y when x = ±w/2:

R

2

sin²φ±wR sinφ+w

2
/4+ y

2 −2R y cosφ+R

2

cos²φ−r

2 = 0

2

or, simplifying

y

2 −2R y cosφ+R

2 −r

2 +w

2
/4±wR sinφ = 0. | (1)

This discriminant of this equation is

∆± = 4R

2

cos²φ∓4wR sinφ−4(R

2 −r

2
)−w

2
. | (2)

Figure 2 shows values of ∆± from (2) as a function of φ. When the hole extends right across the width of the optical beam aperture, there are four intersections between the circle defining the outline of the hole and the outline of the aperture. In this case, ∆+ ≥ 0,∆− ≥ 0. When the outline of the hole intersects with only one vertical side of the optical beam aperture, then there are two intersections between the circle and the outline of the aperture and ∆+ < 0,∆− ≥ 0. When there are no intersections between the circle and the outline of the aperture then both discriminants are negative.
The limits in terms of the angular displacement φ of the ranges with solutions are given by ∆± = 0. From (2), this gives

4R

2

sin²φ±4wR sinφ−4r

2 +w

2 = 0

or

sinφ =

∓4wR ±

p
16w²R² −16R²

(w² −4r

2
)
8R²

sinφ =

∓w ±

p
w² −(w² −4r

2
)
2R

sinφ =

∓w ±2r
2R

sinφ =

∓w/2±r
R

The four limiting values for φ derived from this equation provide the limits of the two intersection and four intersection cases in the positive and negative φ directions. Putting w = 0.5mm, r = 0.5mm and R = 10mm, we get limits of |φ| ≤ 4.30◦ for the two intersections case, and |φ| ≤ 1.43◦
for the four intersections case, which matches with the limits seen in Figure 2.
Solutions to the positive and negative versions of (1) exist when ∆± ≥ 0 and are given by:

y±

± = R cosφ±

1
2

p
∆± = yc±

1
2

p
∆± | (3)

(The sign of the discriminant ∆± matches the sign on the left hand side. The other plus-or-minus sign is for the usual pair of solutions to a quadratic equation, and corresponds to the two members of the pairs of intersection points.) Figure 3 shows these solutions as a function of φ.

3

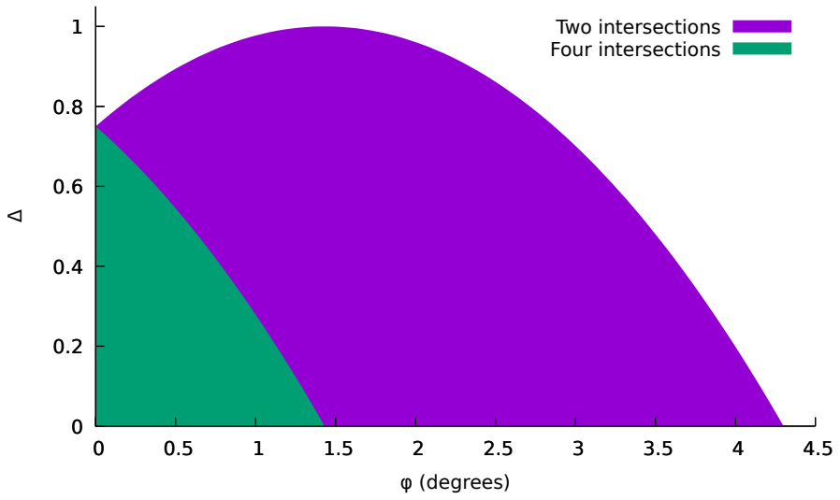
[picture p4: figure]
φ (degrees); Two intersections Four intersections

Figure 2: Discriminant for hole/beam intersection equation as a function of angular displacement φ. The boundary of the “two intersections” region is ∆−(φ), while that of the “four intersections” region is ∆+(φ).

## Hole/aperture overlap area

Given the intersection information from (3), we now need to calculate the area of the overlap between the encoder disk hole and the photointerrupter optical aperture. There are three cases to consider, two requiring calculation and one trivial:

1. There are two intersections between the outline of the hole and the optical aperture. In this case, the overlap between the hole and aperture is formed by a line segment of the vertical side of the aperture and a segment of the circle forming the outline of the hole — this segment lies inside the optical aperture and has endpoints given by the intersection points between the hole and the vertical side of the aperture (Figure 4a).
2. There are four intersections between the outline of the hole and the optical aperture. In this case, the overlap is the encoder disk hole minus two segments of the circle forming the outline of the hole — these segments lie outside the optical aperture and have endpoints given by the intersection points between the hole and the vertical sides of the aperture (Figure 4b).
3. There are no intersections between the outline of the encoder disk hole and the optical aperture. In this trivial case, the overlap area is identically zero.

4

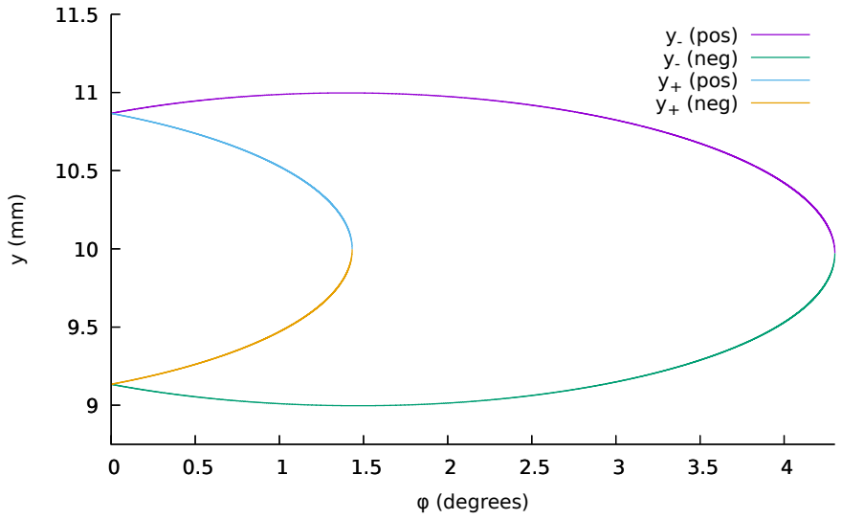
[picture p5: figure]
φ (degrees); y- (pos) y- (neg) y+ (pos) y+ (neg)

Figure 3: Solutions for hole/beam intersection equation as a function of angular displacement φ. The y− values show intersections with the left-hand edge of the optical aperture (remember positive φ means movement of the hole to the left from top dead centre), and y+ values are for intersection with the right-hand edge of the aperture. The “(pos)” and “(neg)” labels indicate the two signs in (3) for the two solutions to each quadratic equation.

In each of the two cases requiring calculation, the calculation can be performed on the basis of an expression for the area of a segment of a circle. For a circle with radius R, the area A of a segment subtending an angle θ at the centre of the circle is
A =

R

2

2

(θ −sinθ). | (4)

Case 1: two intersections

Figure 4a shows this case. The intersection points of the outline of the encoder disk hole and the optical aperture are (−w/2, y

+
−) and (−w/2, y

−
−). We know the
radius of the encoder disk hole, so in order to apply (4) to calculate the area of overlap, we need to find the angle θ. To do this, we construct vectors v+ and v− between the centre of the encoder disk hole and the intersection points:

v+ =

µ
−w/2− xc
y

+
− − yc

¶
, v− =

µ
−w/2− xc
y

−
− − yc

¶
, | (5)

and then
cosθ = vˆ+ · vˆ−.

5

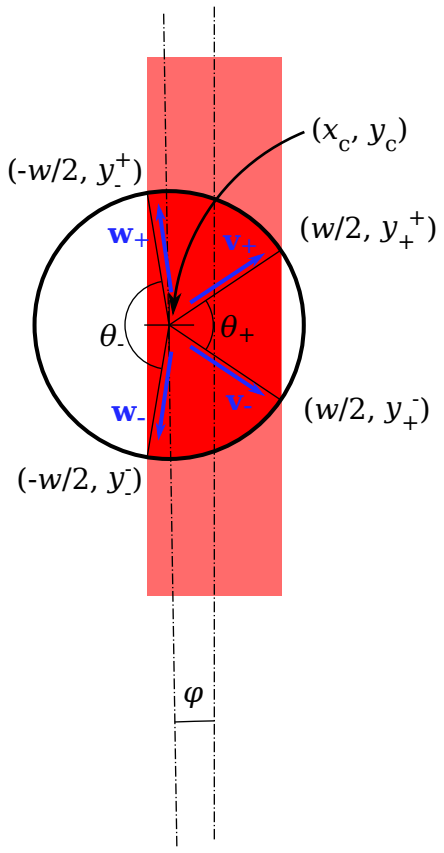
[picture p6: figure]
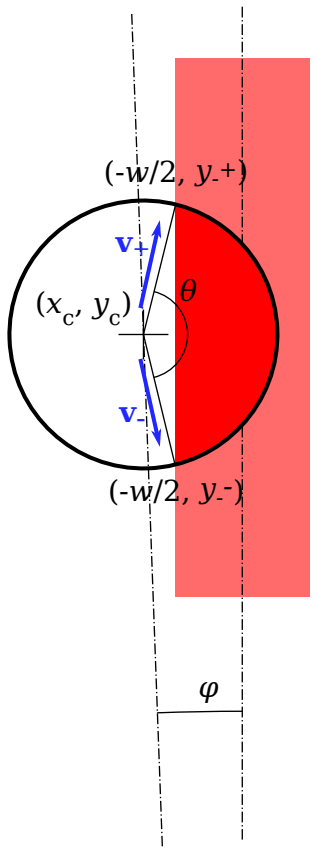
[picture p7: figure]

(a) Two intersections | (b) Four intersections

Figure 4: Overlap cases: (a) two intersections, so overlap is a segment of a circle;
(b) four intersections, so overlap is a circle minus two segments.

6

(Here vˆ is the unit vector in the direction of vector v.) First we calculate v+ · v−, making use of the fact that y

±

− − yc = ±1
2

p
∆− (from (3)):

v+ · v− =

³w
2

+ xc

´2
+(y

+
− − yc )(y

−
− − yc ) =

³w
2

+ xc

´2
−

∆−
4
. | (6)

Now, we also find that

|v±|

2 =

³w
2

+ xc

´2
+(y

±
− − yc )

2
=

³w
2

+ xc

´2
+

∆−
4

so that
|v+||v+| = ³w
2

+ xc

´2
+

∆−
4
and we finally arrive at

cosθ =

v+ · v−
|v+||v+|

=

¡ w
2

+ xc

¢2
−

∆−
4
¡ w
2

+ xc

¢2
+

∆−
4
which gives an area for the two intersection case of

A2 =

r

2

2

(θ −sinθ)

Case 2: four intersections

The four intersections case (Figure 4b) is similar, except that we have two angles, θ− and θ−, one of each side of the optical aperture, and the area of interest is the total area of the encoder disk hole minus the area of the two segments subtended by θ− and θ−.
The left-hand side of Figure 4b can be treated the same way as for the two intersections case:

cosθ− =

w+ ·w−
|w+||w+|

=

¡ w
2

+ xc

¢2
−

∆−
4
¡ w
2

+ xc

¢2
+

∆−
4
. | (7)

The right-hand side goes the same kind of way, with vectors v+ and v− defined as:

v+ =

µ
w/2− xc
y

+
+ − yc

¶
, v− =

µ
w/2− xc
y

−
+ − yc

¶
, | (8)

so that
v+ · v− =

³w
2

− xc

´2
+(y

+
+ − yc )(y

−
+ − yc ) =

³w
2

− xc

´2
−

∆+
4
. | (9)

and

|v±|

2 =

³w
2

− xc

´2
+(y

±
+ − yc )

2
=

³w
2

− xc

´2
+

∆+
4

so that
|v+||v+| = ³w
2

− xc

´2
+

∆+
4

7

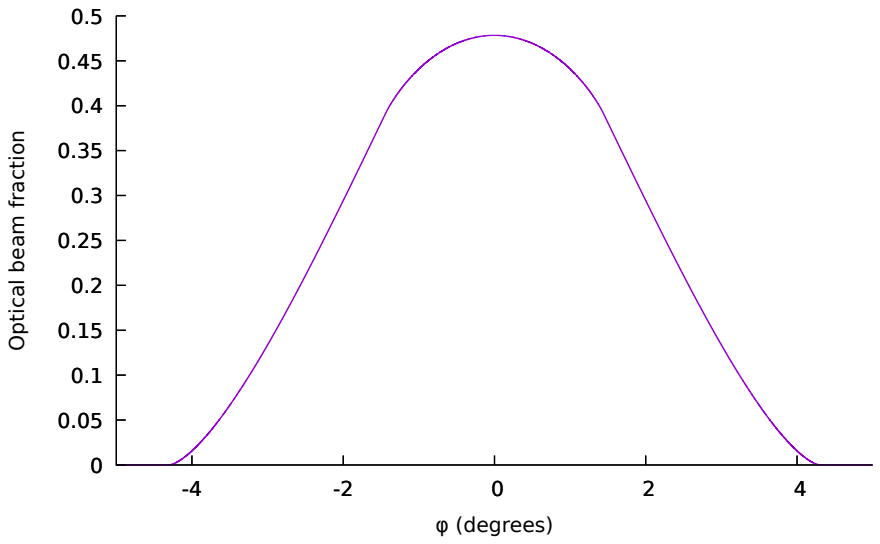
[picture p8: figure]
Optical beam fraction; φ (degrees)

Figure 5: Dependence of fraction of area of photointerrupter optical beam covered by encoder disk hole as a function of angular displacement φ, based on w = 0.5mm, r = 0.5mm and R = 10mm.

and we arrive at

cosθ+ =

v+ · v−
|v+||v+|

=

¡ w
2

− xc

¢2
−

∆+
4
¡ w
2

− xc

¢2
+

∆+
4

The total area in the four intersections case is then:

A4 = πr

2 −

r

2

2

(θ+ −sinθ+)−

r

2

2

(θ− −sinθ−).

## Final results

The functional dependence of the overlap area between an encoder disk hole and the optical beam of the interrupter is shown in Figure 5, representing the overlap as the fraction of the photointerrupter optical beam covered by the encoder hole disk. The assumption is that the current generated by the phototransistor in the photointerrupter will be proportional to this fractional overlap.
We can now use these results to generate simulated photocurrent signals for use in simulations.

8

## Generation of simulated signals

Based on the results so far, we want to be able to generate PWL (piecewise linear) data files for use in LTSpice simulations. We’ll do this with a Python script. Basically, the script just duplicates the calculations performed above, and produces a time series of simulated phototransistor current values, based on a time profile of wheel velocity. We assume that the phototransistor current is proportional to the fraction of the optical aperture that is overlapped by the motor encoder disk hole. The calculations go something like this, stepping the simulation time by a constant timestep (I’ve been using ∆t = 0.1ms):

1. Determine the current linear velocity from the current simulation time. The example I’ve been using starts from rest, accelerates to a constant speed, has a constant velocity segment, then decelerates back to rest. Acceleration and deceleration are both eased using a parabolic easing function.
2. Step the current distance, wheel angle and encoder disk angle using simple Euler integration.
3. Normalise the encoder disk angle into the range |φ| ≤ ∆φ/2, where ∆φ is the angular separation between adjacent holes in the encoder disk.
4. We can then apply the calculations in the first part of this document to the angle φ to get the area overlap fraction between the optical aperture and the hole in the encoder disk.
5. Multiply the area overlap fraction by the maximum light current generated by the phototransistor (I’m using IL(max) = 2mA, which is based on the “typical” value for the Vishay TCST1230 photointerrupter I’m planning to use.)

The results of this procedure are shown in Figure 6.

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
0 | 0.5 | 1 | 1.5 | 2

Current (mA)

Time (s)

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
0 | 0.5 | 1 | 1.5 | 2

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
2 | 2.5 | 3 | 3.5 | 4

Current (mA)

Time (s)

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
2 | 2.5 | 3 | 3.5 | 4

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
4 | 4.5 | 5 | 5.5 | 6

Current (mA)

Time (s)

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
4 | 4.5 | 5 | 5.5 | 6

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
6 | 6.5 | 7 | 7.5 | 8

Current (mA)

Time (s)

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
6 | 6.5 | 7 | 7.5 | 8

Figure 6: Simulated phototransistor current based on using a Vishay TCST1230 photointerrupter, an encoder disk with 32 holes of 1 mm diameter on a 20 mm diameter circle, and a linear velocity profile starting from rest, increasing to 50 mm/s in 3 seconds, travelling at constant speed for 2 seconds, then decelerating back to rest in 3 seconds.

10

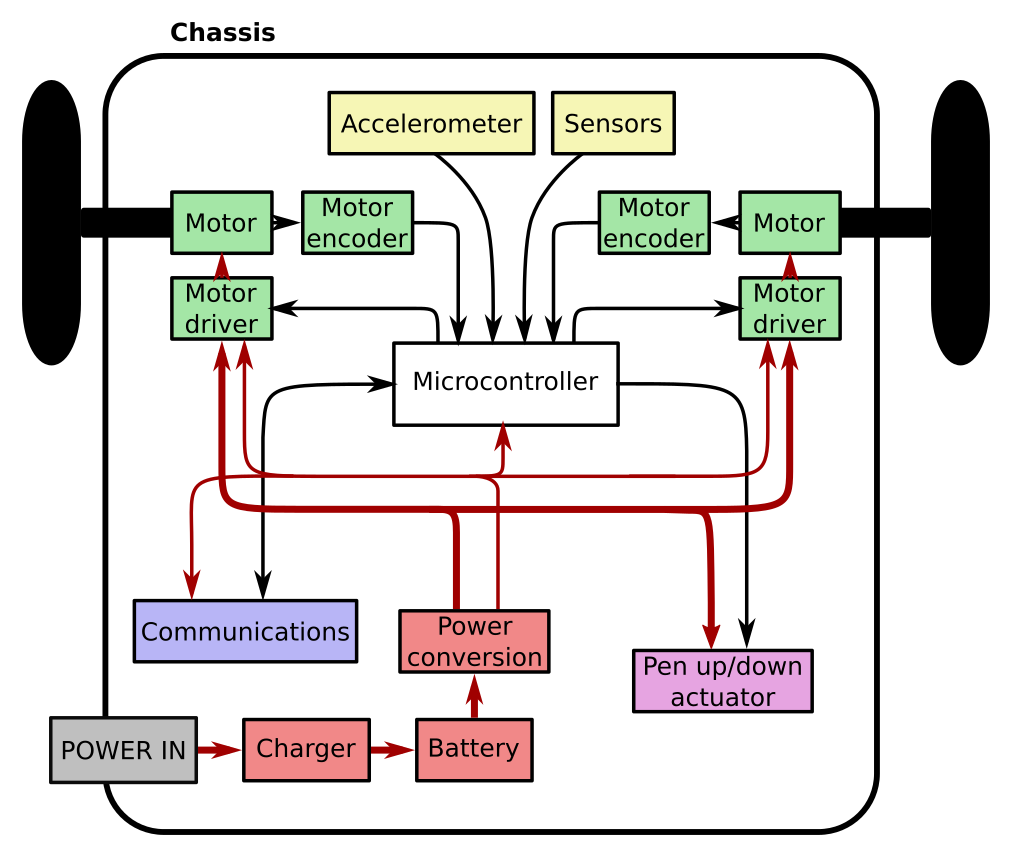
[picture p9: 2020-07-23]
doc/system-block-diagram.png

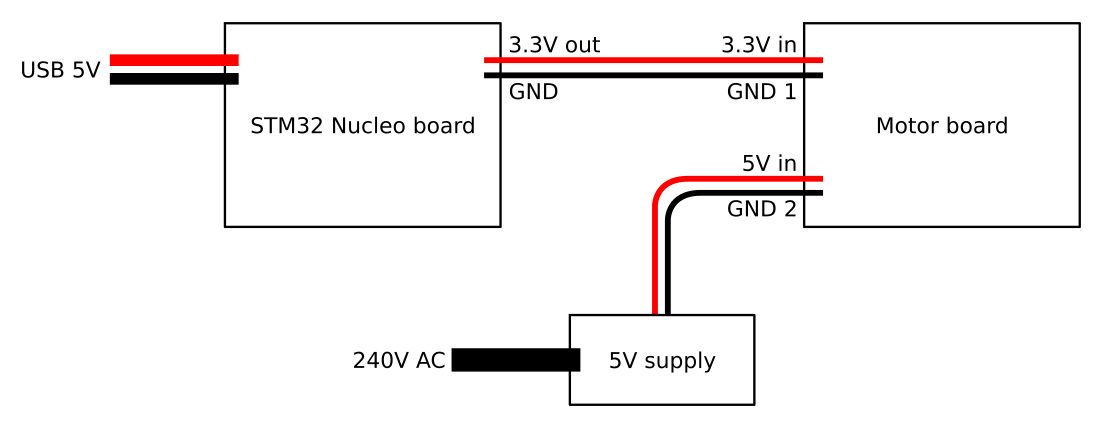
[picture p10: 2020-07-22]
prototypes/motor-board/doc/power-supplies.png

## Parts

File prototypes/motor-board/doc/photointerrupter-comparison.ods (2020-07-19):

ROBOT DIMENSIONS |  |  |  |  |  |  |  |  |  |  |  |  |  |  |  | PHOTOINTERRUPTER DIMENSIONS
Chassis thickness | 1.50 |  |  |  |  |  |  |  |  |  |  |  |  |  |  | L = length perpendicular to slot
Chassis plate separation | 23.00 |  |  |  |  |  |  |  |  |  |  |  |  |  |  | W = width parallel to slot
Hole centre line radius | 10.00 |  | Radius of line of centres of encoder disk |  |  |  |  |  |  |  |  |  |  |  |  | H = total height from PCB
PCB-optical axis distance | 3.00 |  | Distance without PCB-chassis standoff |  |  |  |  |  |  |  |  |  |  |  |  | Ws = slot width
 |  |  |  |  |  |  |  |  |  |  |  |  |  |  |  | Ds = slot depth
Hole-to-edge clearance | 1.25 |  | Distance between centres of encoder disk holes and edge of disk |  |  |  |  |  |  |  |  |  |  |  |  | Do = depth of centre of optical axis
Minimum slot depth | 2.00 |  |  | (C1: interrupter slot must be at least this deep below optical axis, plus some tolerance) |  |  |  |  |  |  |  |  |  |  |  | Wa = aperture width
 |  |  |  |  |  |  |  |  |  |  |  |  |  |  |  | Ha = aperture height
Motor shaft length | 9.00
Motor shaft end spacing | 2.00 |  | Space required between outside edge of encoder disk and end of motor shaft
Encoder disk thickness | 1.00 |  |  | (C2: slot must be at least twice this width) |  |  |  |  |  |  |  |  |  |  |  | (Use M2.5 washers for standoff: 0.5mm thick each.)
Available shaft length | 6.00 |  | C3: distance from outside edge of interrupter to centre of slot must be less than this
Part | Mfr | L | W | H | Ws | Ds | Do | ID / nA | IL(min) / mA | Wa | Ha | C1? | C2? | C3? | OK? | Standoff
TCST1202 | Vishay | 11.90 | 6.30 | 10.80 | 3.10 | 7.70 | 2.60 | 100 | 1.0 (2.0 typ.) | 0.50 | 3.80 | OK | OK | OK | OK | 5.2
TCST1230 | Vishay | 9.20 | 4.80 | 5.40 | 2.80 | 4.40 | 1.70 | 100 | 0.5 (2.0 typ.) | 0.50 | 2.00 | OK | OK | OK | OK | 0.7
TCST1103 | Vishay | 11.90 | 6.30 | 10.80 | 3.10 | 7.70 | 2.60 | 100 | 2.00 | 1.00 | 3.80 | OK | OK | OK | OK | 5.2
TCST1300 | Vishay | 11.90 | 6.30 | 10.80 | 3.10 | 7.70 | 2.60 | 100 | 0.25 | 0.25 | 3.80 | OK | OK | OK | OK | 5.2
EE-SX1018 | Omron | 8.00 | 4.00 | 6.00 | 2.00 | 4.50 | 1.50 | 200 | 0.50 | 0.30 | 1.00 | OK | OK | OK | OK | 1.5
EE-SX1049 | Omron | 9.00 | 4.00 | 5.20 | 2.00 | 3.70 | 1.50 | 200 | 0.50 | 0.50 | 1.00 | OK | OK | OK | OK | 0.7
EE-SX1055 | Omron | 8.90 | 4.00 | 5.40 | 2.80 | 4.40 | 1.50 | 200 | 0.50 | 0.50 | 1.00 | OK | OK | OK | OK | 0.9
EE-SX1106 | Omron | 6.40 | 4.20 | 5.40 | 3.00 | 3.90 | 1.20 | 500 | 0.20 | 0.40 | 1.20 | OK | OK | OK | OK | 1.2
LTH-306-01 | Lite-On | 9.60 | 4.00 | 6.00 | 2.70 | 5.00 | 1.90 | 100 | 5.00 | 0.85 | 0.85 | OK | OK | OK | OK | 1.1
RPI-352 | Rohm | 6.40 | 4.20 | 5.40 | 3.00 | 3.90 | 1.20 | 500 | 0.20 | 0.40 | 1.20 | OK | OK | OK | OK | 1.2
RPI-441C1 | Rohm | 8.00 | 4.20 | 5.20 | 4.00 | 4.20 | 1.20 | 500 | 0.20 | 0.50 | 2.40 | OK | OK | OK | OK | 1
RPI-441C1E | Rohm | 8.00 | 4.20 | 5.20 | 4.00 | 4.20 | 1.20 | 500 | 0.20 | 0.50 | 2.40 | OK | OK | OK | OK | 1
TCST1030 | Vishay | 8.30 | 4.70 | 8.15 | 3.00 | 4.00 | 1.20 | 100 | 1.20 | ? | ? | OK | OK | OK | OK | 3.95
LTH-301-19 | Lite-On | 11.80 | 6.00 | 9.80 | 4.10 | 8.80 | 2.30 | 100 | 0.07 | ? | ? | OK | OK | OK | OK | 4.5
EE-SX1103 | Omron | 5.00 | 4.20 | 5.20 | 2.00 | 2.80 | 1.00 | 500 | 0.50 |  |  | NO | OK | OK | NO
EE-SX1105 | Omron | 4.90 | 2.60 | 3.30 | 2.00 | 2.60 | 1.00 | 500 | 0.20 |  |  | NO | OK | OK | NO
EE-SX198 | Omron | 12.20 | 5.00 | 10.00 | 3.00 | 7.50 | 2.50 | 200 | 0.50 |  |  | OK | OK | NO | NO
EE-SX199 | Omron | 12.20 | 5.00 | 10.00 | 3.00 | 7.50 | 2.50 | 200 | 0.50 |  |  | OK | OK | NO | NO
EE-SX1071 | Omron | 13.60 | 6.20 | 10.20 | 3.40 | 7.20 | 3.00 | 200 | 0.50 |  |  | OK | OK | NO | NO
EE-SJ5-B | Omron | 15.40 | 6.20 | 10.20 | 5.00 | 7.20 | 3.00 | 200 | 0.50 |  |  | OK | OK | NO | NO
EE-SX1041 | Omron | 14.00 | 6.00 | 10.00 | 5.00 | 7.50 | 2.50 | 200 | 0.50 |  |  | OK | OK | NO | NO
EE-SX1042 | Omron | 14.00 | 5.00 | 14.50 | 5.00 | 12.00 | 2.50 | 200 | 0.50 |  |  | OK | OK | NO | NO
EE-SX1081 | Omron | 13.70 | 5.00 | 10.00 | 5.00 | 7.50 | 2.50 | 200 | 0.50 |  |  | OK | OK | NO | NO
EE-SX1115 | Omron | 14.00 |  |  |  |  |  |  |  |  |  | NO | NO | NO | NO
EE-SX1137 | Omron | 13.70 |  |  |  |  |  |  |  |  |  | NO | NO | NO | NO
EE-SX1035 | Omron | 12.60 |  |  |  |  |  |  |  |  |  | NO | NO | NO | NO
EE-SX1070 | Omron | 17.70 |  |  |  |  |  |  |  |  |  | NO | NO | NO | NO
EE-SX1140 | Omron | 23.00 |  |  |  |  |  |  |  |  |  | NO | NO | NO | NO
LTH-301-05 | Lite-On | 14.00 |  |  |  |  |  |  |  |  |  | NO | NO | NO | NO
LTH-301-07 | Lite-On | 14.00 |  |  |  |  |  |  |  |  |  | NO | NO | NO | NO
LTH-301-23 | Lite-On | 13.70 |  |  |  |  |  |  |  |  |  | NO | NO | NO | NO
RPI-221 | Rohm | 4.90 | 2.60 | 3.30 | 2.00 | 2.60 | 1.00 | 500 | 0.20 |  |  | NO | OK | OK | NO
RPI-222 | Rohm | 4.90 | 2.60 | 3.30 | 2.00 | 2.30 | 1.00 | 500 | 0.30 |  |  | NO | OK | OK | NO
RPI-243 | Rohm | 5.00 | 4.20 | 5.20 | 2.00 | 2.80 | 1.00 |  |  |  |  | NO | OK | OK | NO
RPI-246 | Rohm | 5.00 | 4.20 | 5.20 | 2.00 | 2.80 | 1.00 |  |  |  |  | NO | OK | OK | NO

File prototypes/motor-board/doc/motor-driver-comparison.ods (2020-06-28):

 |  |  |  |  |  |  |  | * means only in current regulation modes
 |  |  |  |  |  |  |  | ↓
Manufacturer | Part | Channels | Supply voltage (logic/motor) | Max. drive current / ch. | Modes | Interface | PWM? | Current sense | Protection (fault pin) | Packages | Price | Comments
TI | DRV8833C | 2 | 2.7 – 10.8 V | 0.7 A | 1, 5 | IN1, IN2 (x2) | Y | * | V-, C, T | HTSSOP-16 | 1.59
TI | DRV8833 | 2 | 2.7 – 10.8 V | 0.5 A | 1, 5 | IN1, IN2 (x2) | Y | * | V-, C, T | TSSOP-16 | 1.59
TI | DRV8847 | 2 | 2.7 – 18 V | 1 A | 1, 9, 10 | IN1, IN2 (x2) | Y | * | V-, C, S, T | TSSOP-16 | 1.73 | Multiple interface options: “4-pin mode” is right for MM
Toshiba | TB67H450FNG | 1 | 4.5 – 44 V | 1.5 A | 1, 10 | IN1, IN2 | Y | * | V-, C, T | HSOP-8 | 1.38
Diodes Inc | ZXBM5210 | 1 | 3 – 18V | 1.5 A | 1, 2 | FWD, REV | Y | ? | V+, V-, C, T | SO-8 | 0.97 | Dead time for direction reversal (3us)
Maxim | MAX14871 | 1 | 4.5 – 36V | 2.8 A | 1, 3, 4, 5, 6 | ~EN, PWM, DIR | Y | ? | V-, C, T | TSSOP-16 (EP) | 2.93 | Dead time for direction reversal (140ns)
TI | DRV8848 | 2 | 4 – 18 V | 1 A | 1, 9, 10 | IN1, IN2 (x2) | Y | * | V-, C, S, T | HTSSOP-16 | 2.39
ST | STSPIN250 | 1 | 1.8 – 10V | 2.6 A | 5 | ~EN, PH, PWM | Y | ? | V+, C, S, T | QFN-16 | 1.78
TI | DRV8832 | 1 | 2.75 – 6.8V | 1 A | 1, 7 | IN1, IN2 | Y | Y | V-, C, S, T | MSOP-10, VSON-10 | 1.86 | Uses high-side FETs for slow decay
TI | DRV8837C | 1 | 1.8 – 7 V / 0 – 11 V | 1 A | 1 | IN1, IN2 | Y | N | V-, C, T | WSON-8 | 0.75
TI | DRV8837 | 1 | 1.8 – 7 V / 0 – 11 V | 1.8 A | 1 | IN1, IN2 | Y | N | V-, C, T | WSON-8 | 1.10
TI | DRV8838 | 1 | 1.8 – 7 V / 0 – 11 V | 1.8 A | 8 | PH, EN | N? | N | V-, C, T | WSON-8 | 1.10
Toshiba | TC78H600FTG | 2 | 2.7 – 5.5 V / 2.5 – 15 V | 0.8 A | 1, 10 | IN1, IN2, PWM (x2) | Y | * | V-, C, T | QFN-24 | 1.62
TI | DRV8835 | 2 | 2 – 7 V / 0 – 11 V | 1.5 A | 1 | IN1, IN2 or PH, EN (x2) | Y | N | V-, C, S, T | WSON-12
TI | DRV8836 | 2 | 2 – 7 V | 1.5 A | 1 | IN1, IN2 or PH, EN (x2) | Y | N | V-, C, S, T | WSON-12
Toshiba | TC78H651AFNG | 2 | 1.8 – 7.5 V | 2.0 A | 1 | IN1, IN2 (x2) | Y | N | V-, C, T | TSSOP-16
Toshiba | TC78H660FTG | 2 | 2.5 – 16 V | 2.0 A | ? | IN1, IN2 or PH, EN (x2) | Y |  | V-, C, T | QFN-16
Rohm | BD60203EFV | 2 | 8 – 28V | 1.7 A |  |  | Y | ? | n/a
TI | DRV8871 | 1 | 6.5 – 45 V | 3.6 A |  |  | Y | ? | n/a | HSOP-8
Toshiba | TB6552FTG | 1 | 5 V / 4.5 – 38 V | 3 A | 1, 5 | IN1, IN2 | Y |  | V-, C, T | QFN-24 |  | Toshiba datasheets not as good as TI’s
Toshiba | TB6559FG | 1 | 10 V – 30 V
Toshiba | TB6641FTG | 1 | 10 V – 45 V
Toshiba | TB67H301FTG | 1 | 5 V / 4.5 – 38 V
Operating modes
1: Standard PWM operation (2-pin: 1 H, 1 PWM)
2: On/off with fixed PWM duty cycle (speed control from reference voltage)
3: External current regulation with current sense resistor
4: Internal current regulation (fixed off time, fast decay)
5: Internal current regulation (fixed off time, slow decay)
6: Internal current regulation (25% ripple regulation)
7: Constant voltage regulation
8: On/off only, with no current regulation
9: Forward/reverse only with or without current regulation
10: Internal current regulation (fixed off time, mixed decay)

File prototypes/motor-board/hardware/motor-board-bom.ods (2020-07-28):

MPN | Quantity | Reference | Value | Footprint | Datasheet
EEE-HC1C101XP | 1 | C1 | 100U | mini-mapper:CP_Elec_6.3x7.7 | https://www.mouser.at/datasheet/2/315/ABA0000C1160-947462.pdf
885012207098 | 4 | C2 C5 C6 C7 | 0.1U | mini-mapper:C_0805 | http://datasheet.octopart.com/885012207098-W%C3%BCrth-Elektronik-datasheet-137006532.pdf
885012107015 | 2 | C3 C4 | 1U | mini-mapper:C_0805 | http://datasheet.octopart.com/885012107015-W%C3%BCrth-Elektronik-datasheet-82513951.pdf
PJ-063AH | 1 | J1 | PJ-063AH | mini-mapper:BarrelJack_CUI_PJ-063AH_Horizontal | https://www.mouser.at/datasheet/2/670/pj-063ah-1778660.pdf
SLW-102-01-T-S | 1 | J2 | Conn_01x02 | mini-mapper:PinSocket_1x02_P2.54mm_Vertical | https://www.mouser.at/datasheet/2/527/slw-1370256.pdf
22-28-4060 | 1 | J3 | PinHeader_01x06 | mini-mapper:PinHeader_1x06_P2.54mm_Vertical | https://www.mouser.at/datasheet/2/276/0022284060_PCB_HEADERS-228129.pdf
CRGP0805F56K | 1 | R1 | 56K | mini-mapper:R_0805 | http://datasheet.octopart.com/CRGP0805F56K-TE-Connectivity-datasheet-114718804.pdf
CRCW080582R0FKEA | 1 | R10 | 82 | mini-mapper:R_0805 | https://www.mouser.at/datasheet/2/427/dcrcwe3-1762152.pdf
CRCW08055K60FKEAC | 1 | R11 | 5.6K | mini-mapper:R_0805 | https://www.mouser.at/datasheet/2/427/crcwce3-1762584.pdf
RL0805FR-070R4L | 1 | R2 | 400m | mini-mapper:R_0805 | https://www.mouser.at/datasheet/2/447/PYu-RL_Group_521_RoHS_L_2-1131815.pdf
CRCW080512K0FKEA | 1 | R3 | 12K | mini-mapper:R_0805 | https://www.mouser.at/datasheet/2/427/dcrcwe3-1762152.pdf
CRCW080516K0FKEA | 1 | R4 | 16K | mini-mapper:R_0805 | https://www.mouser.at/datasheet/2/427/dcrcwe3-1762152.pdf
CRCW0805330KFKEA | 1 | R5 | 330K | mini-mapper:R_0805 | https://www.mouser.at/datasheet/2/427/dcrcwe3-1762152.pdf
CRGP0805F220K | 1 | R6 | 220K | mini-mapper:R_0805 | http://datasheet.octopart.com/CRGP0805F220K-TE-Connectivity-datasheet-114718804.pdf
CRCW0805240KFKEA | 1 | R7 | 240K | mini-mapper:R_0805 | https://www.mouser.at/datasheet/2/427/dcrcwe3-1762152.pdf
CRGP0805F1K0 | 3 | R8 R12 R13 | 1K | mini-mapper:R_0805 | http://datasheet.octopart.com/CRGP0805F1K0-TE-Connectivity-datasheet-114718804.pdf
CRCW08057K50FKEA | 1 | R9 | 7.5K | mini-mapper:R_0805 | https://www.mouser.at/datasheet/2/427/dcrcwe3-1762152.pdf
TLV70245DBVR | 1 | U1 | TLV70245_SOT23-5 | mini-mapper:SOT-23-5 | http://www.ti.com/lit/ds/symlink/tlv702.pdf
TB67H450FNG | 1 | U2 | TB67H450FNG | mini-mapper:SOIC127P600X175-9N | https://www.mouser.com/pdfDocs/TB67H450FNG_datasheet_en_20190401.pdf
TLV9051IDBVR | 1 | U3 | TLV9051 | mini-mapper:SOT-23-5 | https://www.ti.com/lit/ds/symlink/tlv9052.pdf
LMV331IDBVR | 1 | U4 | LMV331 | mini-mapper:SOT-23-5 | http://www.ti.com/lit/ds/symlink/lmv331.pdf
TCST1202 | 1 | U5 | TCST1202 | mini-mapper:TCST1202 | https://www.vishay.com/docs/83764/tcst1103.pdf
907-5MM | 4 | n/a | Spacer: 5mm | n/a | https://www.mouser.at/datasheet/2/50/9XX-XXX-880271.pdf
29304 | 4 | n/a | M2.5 x 12 screws | n/a | https://www.mouser.at/datasheet/2/215/9304-745754.pdf
16M02556080 | 4 | n/a | M2.5 washers | n/a | https://www.mouser.at/ProductDetail/Essentra/16M02556080
04M025045HN | 4 | n/a | M2.5 nuts | n/a | https://www.mouser.at/ProductDetail/Essentra/04M025045HN
n/a | 4 | H1 H2 H3 H4 | MountingHole | mini-mapper:MountingHole_2.7mm_M2.5 | n/a
n/a | 1 | TP1 TP2 TP3 TP4 | TestPoint | mini-mapper:TestPoint_Pad_2.0x2.0mm | n/a

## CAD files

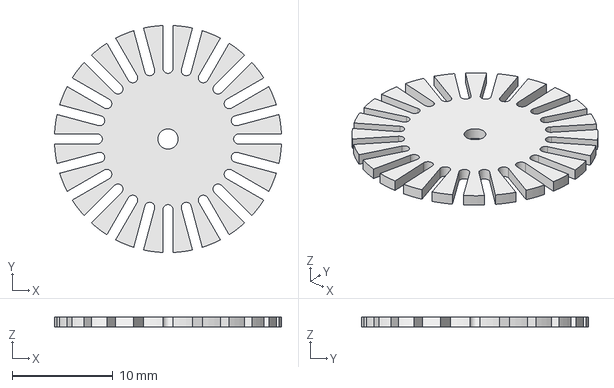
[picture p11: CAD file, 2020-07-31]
mech/slotted-motor-encoder-disk.FCStd
22.5 x 22.5 x 1.00 mm

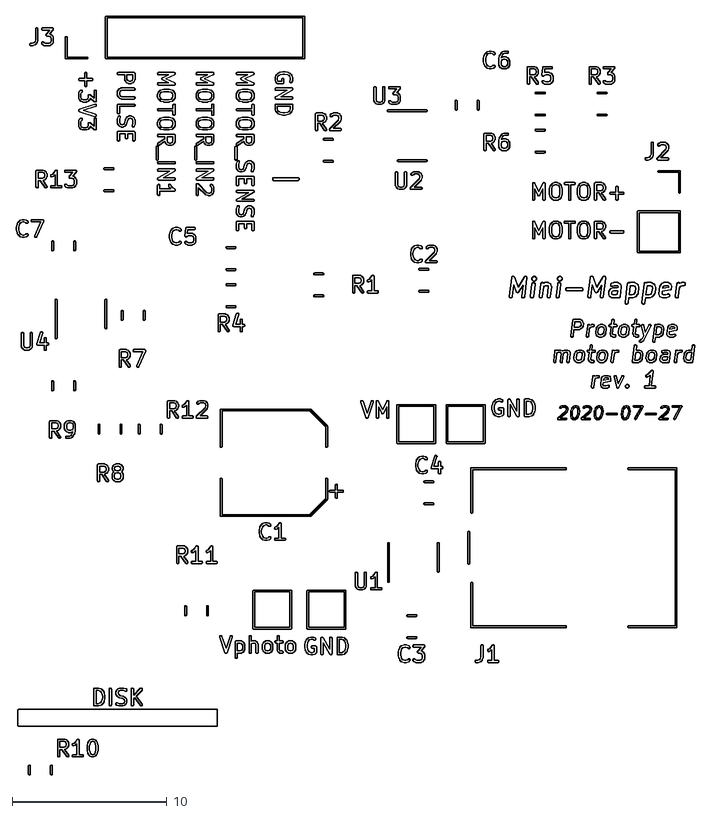
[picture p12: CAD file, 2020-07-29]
prototypes/motor-board/doc/motor-prototype-setup/front-silk.dxf
43.9 x 49.1

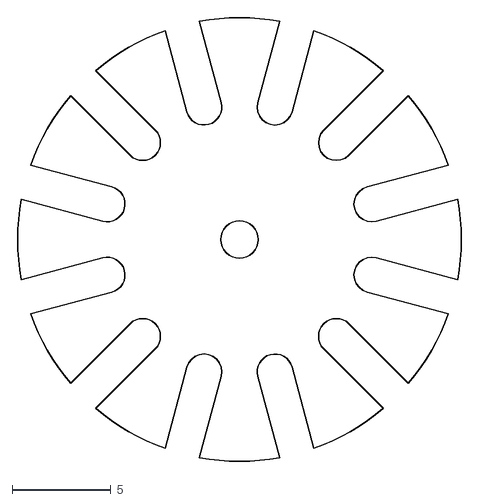
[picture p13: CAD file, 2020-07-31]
prototypes/motor-board/motor-encoder-disk/v2/encoder-disk-outline.dxf
22.6 x 22.6

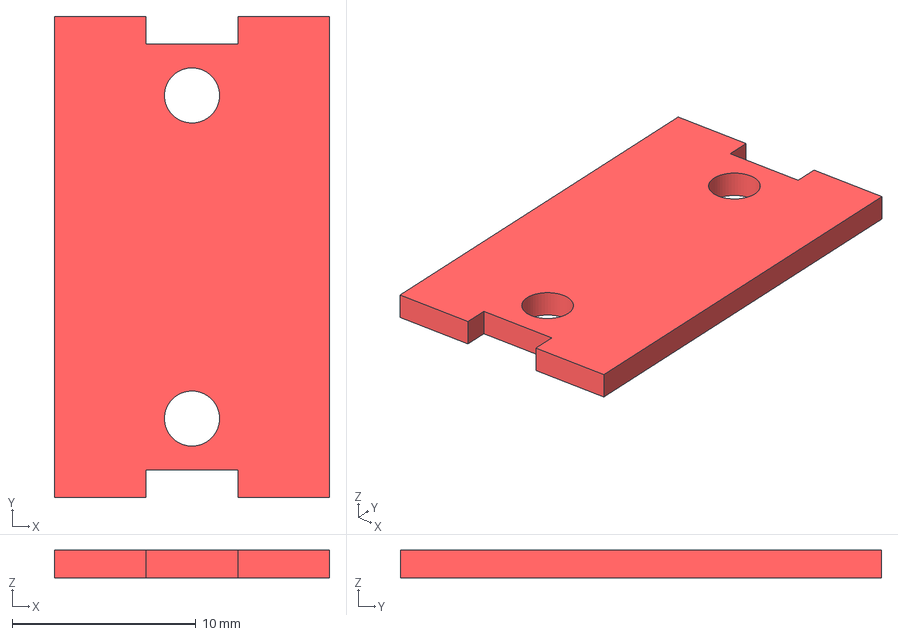
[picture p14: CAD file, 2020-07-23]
mech/motor-mount-bracket.FCStd
15.0 x 26.2 x 1.50 mm

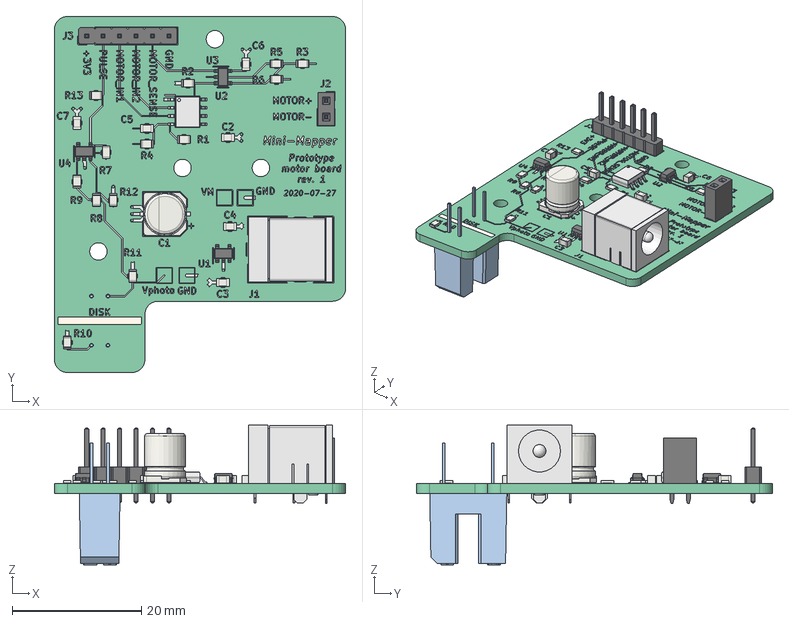
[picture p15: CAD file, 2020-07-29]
prototypes/motor-board/doc/motor-prototype-setup/motor-board.FCStd
45.0 x 55.0 x 21.6 mm
Pcb_1a2f
topTracks_1a2f
botTracks_1a2f
topSilks_ae8c
R13_R_0805_2012Metric_5F200653
R10_R_0805_2012Metric_5F1EEDF4
C1_CP_Elec_63x77_5F1E4373
C2_C_0805_2012Metric_5F1E440A
C3_C_0805_2012Metric_5F1E4066
C4_C_0805_2012Metric_5F1E4096
C5_C_0805_2012Metric_5F1E5886
C6_C_0805_2012Metric_5F1B546C
C7_C_0805_2012Metric_5F1B633B
J1_BarrelJack_CUI_PJ-063AH_Horizontal_5F1E3BF7
J2_PinSocket_1x02_P254mm_Vertical_5F1B54B0
J3_PinHeader_1x06_P254mm_Vertical_5F1EDC8F
R1_R_0805_2012Metric_5F1B54F1
R2_R_0805_2012Metric_5F1B5502
R3_R_0805_2012Metric_5F1B5513
R4_R_0805_2012Metric_5F1E5733
R5_R_0805_2012Metric_5F1B5535
R6_R_0805_2012Metric_5F1B5546
R7_R_0805_2012Metric_5F1B5557
R8_R_0805_2012Metric_5F1E425A
R9_R_0805_2012Metric_5F1B5579
R11_R_0805_2012Metric_5F1B559B
R12_R_0805_2012Metric_5F1B55AC
U1_SOT_23_5_5F1E402E
U2_TB67H450FNG,EL_5F1B55E7
U3_SOT_23_5_5F1E492E
U4_SOT_23_5_5F1B5611
U5_GO-100198.0_5F1B5632

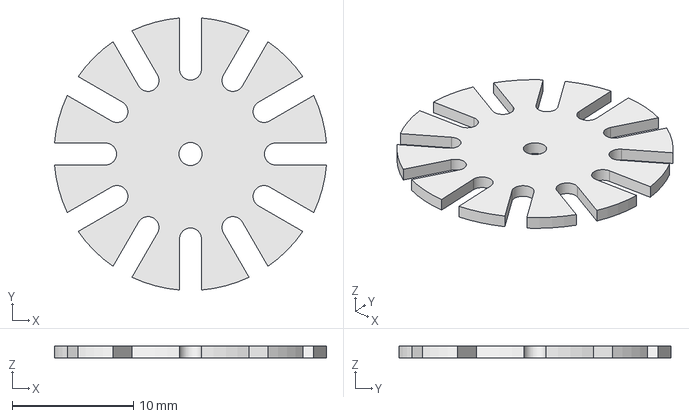
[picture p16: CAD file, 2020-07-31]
prototypes/motor-board/motor-encoder-disk/v2/slotted-motor-encoder-disk-2.FCStd
22.4 x 22.4 x 1.00 mm

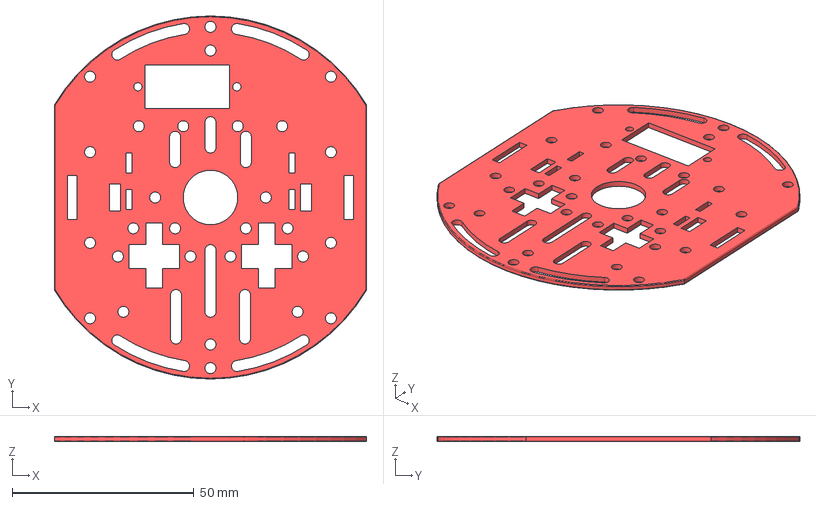
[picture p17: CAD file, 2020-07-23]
mech/chassis-plate.FCStd
86.0 x 100.0 x 1.50 mm

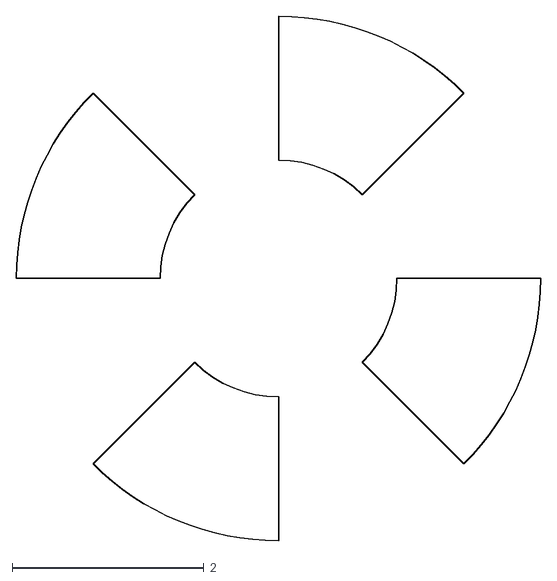
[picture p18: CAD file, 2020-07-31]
prototypes/motor-board/motor-encoder-disk/v2/spinner.dxf
5.47 x 5.47

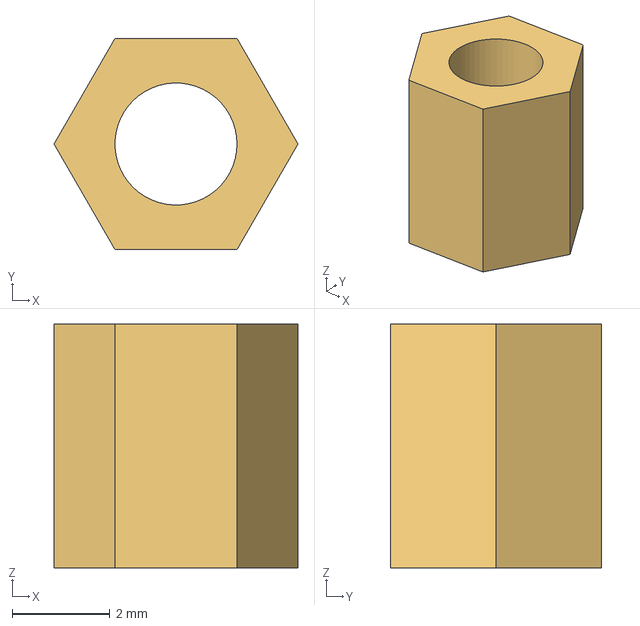
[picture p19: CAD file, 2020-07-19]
mech/pcb-standoff-5mm.FCStd
5.00 x 4.33 x 5.00 mm

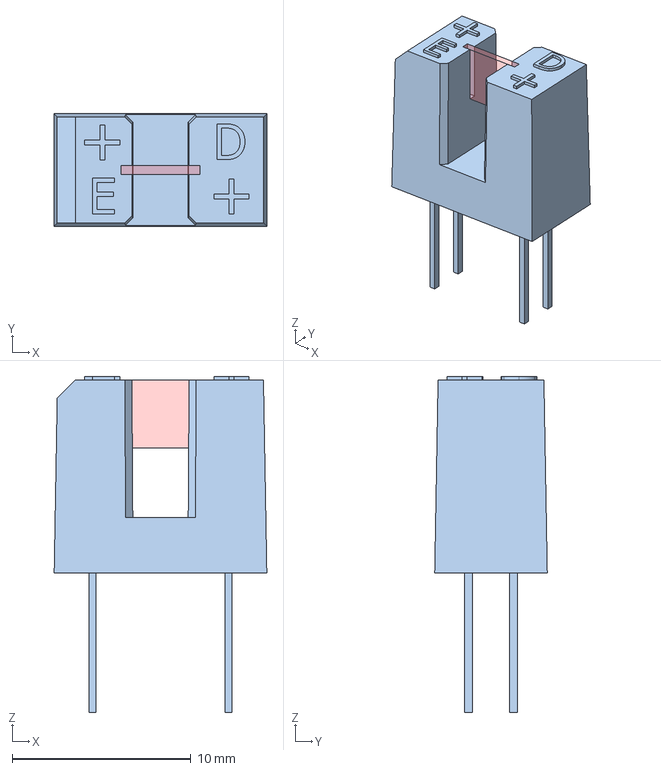
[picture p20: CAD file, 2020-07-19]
mech/photointerrupter-vishay-tcst1202.FCStd
11.9 x 6.30 x 18.8 mm
GO-100198.0

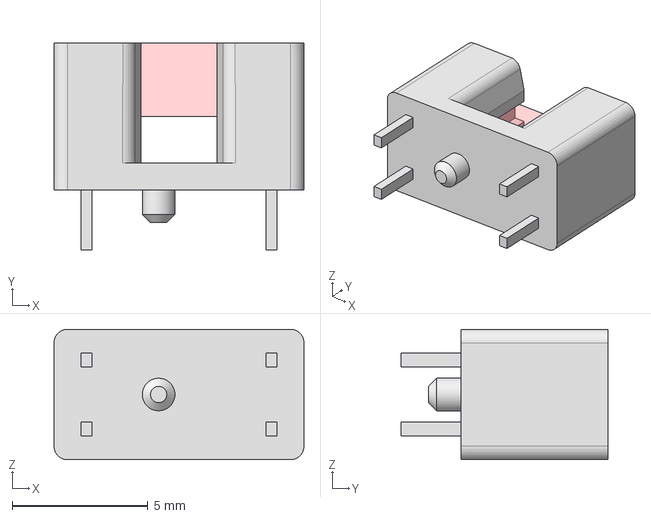
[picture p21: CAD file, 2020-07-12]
mech/photointerrupter-vishay-tcst1230.FCStd
9.20 x 7.60 x 4.80 mm
AK-21.0006.00

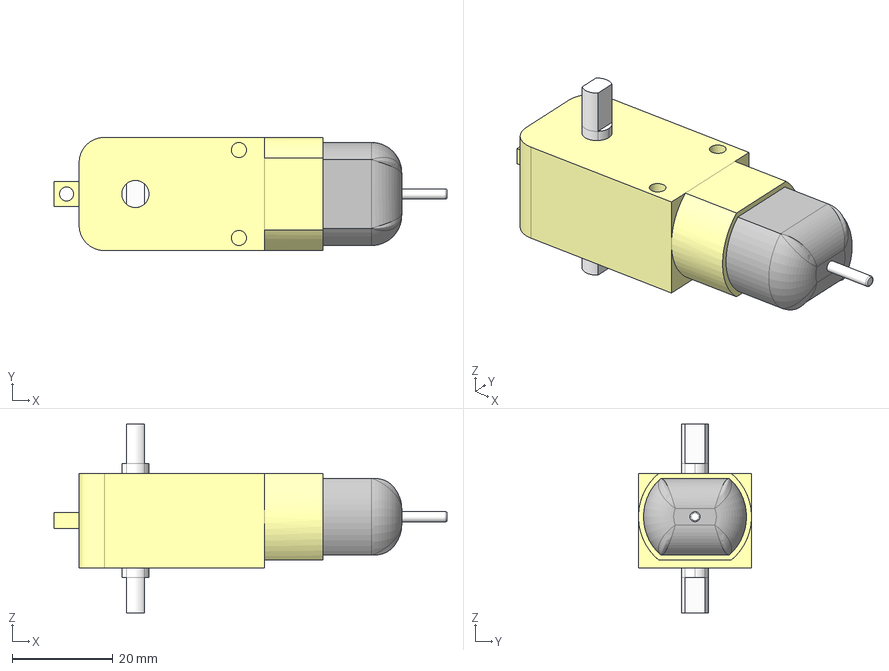
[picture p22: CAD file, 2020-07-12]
mech/motor.FCStd
78.2 x 22.5 x 37.6 mm
MotorShaft
MotorBody
GearboxBody
OutputShaft

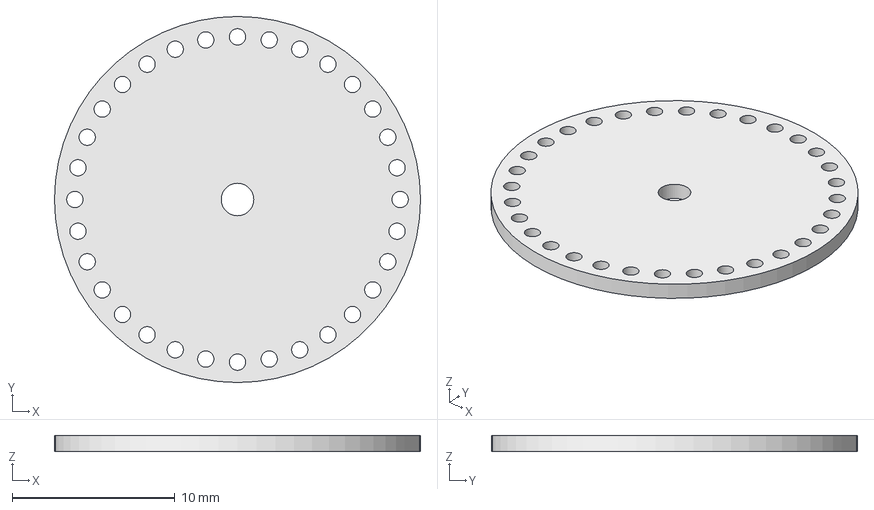
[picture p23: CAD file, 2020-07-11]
mech/motor-encoder-disk.FCStd
22.5 x 22.5 x 1.00 mm

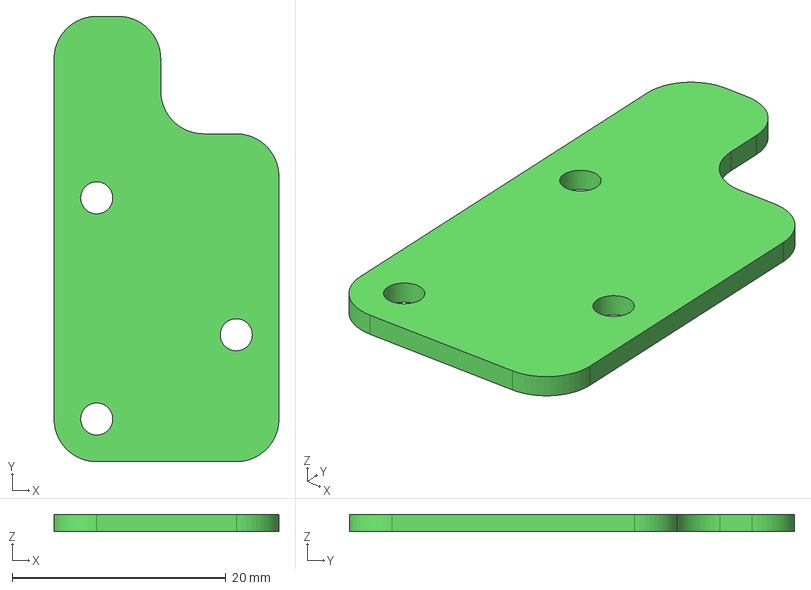
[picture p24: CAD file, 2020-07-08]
mech/motor-proto-pcb.FCStd
21.1 x 41.7 x 1.60 mm

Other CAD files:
prototypes/motor-board/hardware/mechanical-interface.FCStd
prototypes/motor-board/motor-encoder-disk/motor-encoder-disk-outline.FCStd
mech/pcb-standoff-3mm.FCStd
mech/photo-interrupter.FCStd
mech/castor.FCStd
mech/washer-m2.5.FCStd
mech/wheel-rim.FCStd
prototypes/motor-board/hardware/mechanical-interface.dxf
prototypes/motor-board/motor-encoder-disk/v1/encoder-disk-outline.dxf

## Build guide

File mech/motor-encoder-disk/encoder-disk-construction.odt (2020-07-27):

Motor encoder disks

1. Cut 25 mm strips from material.
2. Cut 25 mm x 25 mm squares from material (6 off).
3. Make two stacks of 3 squares, stacking with double-sided tape (one working stack, one for spacing).
4. Cover top of working stack with permanent marker.
5. Find centre of working stack and mark with pin.
6. Draw circles on working stack with compass with pin: 11.25 mm radius and 10.00 mm radius.
7. Push pin through centre of working stack (1 mm stick-out).
8. Put double-sided tape on bottom of working stack.
9. Align working stack on template using pin for centring.
10. Attach working stack to template with pre-placed double-sided tape.
11. Stick spacing stack to back of steel rule.
12. Mark hole centres on working stack: one end of steel rule against pin in centre of working stack, other end against knife or pin aligned in template, mark centre with knife, then mark centre with pin.
13. Remove template and centre pin from working stack and stick working stack to waste.
14. Drill circle of holes (1 mm) through working stack using pin marks for placement.
15. Drill centre hole (1.5 mm) through working stack.
16. Remove working stack from backing waste.
17. Hand sand outer profile of working stack to within 0.5 mm.
18. Tape working stack to 1.5 mm drill bit and use drill to rotary sand working stack to size and circularity.
19. Disassemble working stack and clean up encoder disks.

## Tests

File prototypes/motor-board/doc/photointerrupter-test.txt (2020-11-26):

 - Current limiting resistor on IR LED = 81.7 Ohm
 - Detector resistor = 5.7 k Ohm
 - Supply voltage = 3.313 V
 - "Light" voltage = 3.221 V
 - "Dark" voltage = 0.9 mV - 91.1 mV (depends on exact location of
   occluder and amount of ambient radiation excluded)

=>

 - Light current = 56.5 mA
 - Dark current = 0.158 - 15.9 uA

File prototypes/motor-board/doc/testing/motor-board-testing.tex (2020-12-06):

\documentclass[a4paper,11pt]{article}

\usepackage[utf8]{inputenc}
\usepackage{fourier}
\usepackage{amsmath,amssymb}
\usepackage{xstring,ifthen,xcolor}
\usepackage{xspace}
\usepackage{url}

\usepackage{color}
\definecolor{orange}{rgb}{0.75,0.5,0}
\definecolor{magenta}{rgb}{1,0,1}
\definecolor{cyan}{rgb}{0,1,1}
\definecolor{grey}{rgb}{0.25,0.25,0.25}
\newcommand{\outline}[1]{{\color{grey}{\scriptsize #1}}}
\newcommand{\todo}[1]{{\color{red}\textit{\textbf{#1}}}}
\newcommand{\note}[1]{{\color{blue}\textit{\textbf{#1}}}}
\newcommand{\citenote}[1]{{\color{orange}{[\textit{\textbf{#1}}]}}}

\usepackage{tikz}
\usepackage{pgfmath}
\usetikzlibrary{calc,shapes,positioning}

\title{Mini-Mapper motor prototype board testing}
\author{Ian~Ross}

\graphicspath{{figs/}}

\begin{document}

\maketitle

This document reports testing of the motor prototype board:

\begin{enumerate}
  \item{Basic tests of the electronics by driving the PWM inputs on
    the board using the Analog Discovery 2, and using the logic
    analyser and scope functions of the AD2 to monitor the motor
    encoder and torque measurement outputs.}
  \item{Tests of the software running on the STM32F767ZI Nucleo-144
    board, connected to the Analog Discovery 2 to monitor PWM outputs
    and provide synthetic inputs for the motor encoder and torque
    measurement code.}
  \item{``Live'' testing of the software, connecting the motor board
    to the Nucleo-144 board.}
\end{enumerate}

The software used for these tests is the \texttt{shell-motor}
application, which provides a command line interface for basic motor
operations. (Once this is all working, the emphasis will shift to
using a Python test bench GUI on a PC to talk to driver code on the
Nucleo board.)

\section{Motor board initial testing}

\subsection*{Setup}

The motor board and AD2 are set up as follows for this series of
tests:
\begin{itemize}
  \item{Connect 5V wall wart power supply to motor board.}
  \item{Connect 3.3V supply from AD2 to motor board.}
  \item{Configure two AD2 digital outputs for \texttt{MOTOR\_IN1} and
    \texttt{MOTOR\_IN2}.}
  \item{Configure AD2 digital input for \texttt{PULSE}.}
  \item{Configure AD2 analog input for \texttt{MOTOR\_SENSE}.}
\end{itemize}

The initial protocol for testing here was something like this:
\begin{enumerate}
  \item{Remove 5V power from motor board.}
  \item{Disconnect \texttt{MOTOR\_IN1} and \texttt{MOTOR\_IN2} from
    motor board.}
  \item{Configure AD2 digital outputs in ``Patterns'' panel and
    check.}
  \item{Connect \texttt{MOTOR\_IN1} and \texttt{MOTOR\_IN2} to motor
    board.}
  \item{Apply 5V power to motor board.}
  \item{Run AD2 digital output waveform generator.}
  \item{Record results: motor motion, \texttt{PULSE} and
    \texttt{MOTOR\_SENSE} inputs.}
\end{enumerate}

The control states I tested with this setup were:
\begin{center}
  \begin{tabular}{lcc}
    \textbf{State} & \textbf{\texttt{MOTOR\_IN1}} &
    \textbf{\texttt{MOTOR\_IN2}} \\

    Motor halted   & HIGH           & HIGH \\
    Forward 10\%   & HIGH           & PWM: 10\% LOW \\
    Forward 50\%   & HIGH           & PWM: 50\% LOW \\
    Forward 100\%  & HIGH           & LOW \\
    Backward 10\%  & PWM: 10\% LOW  & HIGH \\
    Backward 50\%  & PWM: 50\% LOW  & HIGH \\
    Backward 100\% & LOW            & HIGH
  \end{tabular}
\end{center}

\subsection*{Results}

\begin{itemize}
  \item{Quite shockingly, everything worked first time!}
  \item{After the initial setup, I didn't bother too much with the
    protocol above, just switching the PWM duty cycle in the AD2
    ``Patterns'' panel. (Which is a more realistic test than I was
    originally planning to do anyway.)}
  \item{The results were pretty much perfect, as far as I can tell.
    There are only two things that might need some attention.}
  \item{Pulse times from the motor encoder might need some smoothing,
    because the encoder disk isn't quite straight.}
  \item{The signal from the motor coil current sense amplifier that
    I'm going to use for torque measurements is quite noisy, but that
    may just be due to seeing the PWM switching frequency coming
    through into the motor coil current.}
  \item{But: PWM speed control works, forwards and backwards; the
    pulse output from the motor encoder works; and torque measurement
    ``works'', though I need to figure out exactly what I'm seeing
    there.}
\end{itemize}

A better solution for the wobble in the motor encoder signal is
probably to correct the mounting of the encoder disk to the motor
shaft. I designed the hole in the encoder disk under-size to ensure a
tight fit, but it's \emph{too} tight because the encoder disks are
manufactured as PCBs and have two layers of copper with no relief
around the mounting hole. That means that it's not possible to push
the encoder disk onto the motor shaft without expanding the hole in
the disk. I did that in a not very careful way for the disk I'm
currently using, but I have two others, and could try to drill an
accurate 2\,mm hole in them to fit exactly the diameter of the motor
shaft (and then glue them in place).

As for what's going on with the motor coil current signal, I need to
investigate that in more detail, but there is at least something
reasonable there, and the DC level of the signal does go up and down
as the motor drive PWM duty cycle is set to higher and lower values.

\section{Software testing}

\subsection*{Setup}

The Nucleo board and AD2 are set up as follows for this series of
tests:
\begin{itemize}
  \item{Connect ground between Nucleo board and AD2.}
  \item{Connect \texttt{PE5} and \texttt{PE6} on Nucleo
    (\texttt{MOTOR\_IN1} and \texttt{MOTOR\_IN2} motor PWM outputs) to
    logic pins 0 and 1 (inputs) on the AD2.}
  \item{Connect \texttt{PB10} on Nucleo (\texttt{PULSE} motor encoder
    input) to logic pin 2 (output) on AD2.}
  \item{Connect \texttt{PA4} on Nucleo (\texttt{MOTOR\_SENSE} analogue
    torque input) to AD2 analogue waveform output W1.}
\end{itemize}

The idea here is for the software on the Nucleo board to drive the PWM
motor driver signals and for these to be observed by the AD2's logic
analyser. The motor encoder input to the Nucleo board will be driven
by the AD2's pattern generator, and the analogue torque input to the
Nucleo board will be driven by the AD2's signal generator.

The AD2 Waveforms software should be configured as follows:
\begin{itemize}
  \item{Logic analyser with inputs 1 and 2 for motor PWM signals from
    Nucleo board.}
  \item{Pattern generator to logic pin 3 for variable frequency square
    wave to drive motor encode input on Nucleo board.}
  \item{Signal generator to output W1 to drive motor torque
    measurement input on Nucleo board.}
\end{itemize}

Test command script:
\begin{verbatim}
# Ensure initial state and command processing OK.

stop

# Test basic motor commanding.

forward 10
stop
reverse 10
stop

# Test torque measurement.

torque on

# Modify DC level of analogue output from AD2 signal generator to test
# different motor coil current levels.

set torque-interval 5000
set torque-interval 500
torque off

# Test motor speed encoder.

encoder on

# Modify frequency of square wave output from AD2 pattern generator to
# test different motor speed measurements.

set encoder-interval 5000
set encoder-interval 500
encoder off
\end{verbatim}

\subsection*{Results}

\begin{itemize}
  \item{\texttt{stop} gives: DIO0 low, DIO1 high. (WRONG: should be
    both high.)}
    \item{\texttt{forward 10} gives: DIO0 high, DIO1 high. (WRONG: should be
    both DIO0 high, DIO1 PWM.)}
    \item{\texttt{reverse 10} gives: DIO0 PWM, DIO1 high. (WRONG: should be
    both high.)}
\end{itemize}

\subsection{PWM shell regression testing}

\begin{center}
  \begin{tabular}{lccc}
    \textbf{Register} & \textbf{Old: works} & \textbf{New: broken} & \textbf{Status} \\
    \textbf{\texttt{RCC}} \\
    \texttt{AHB1ENR} & \texttt{0x30000a} & \texttt{0x30000f} & OK \\
    \texttt{APB1ENR} & \texttt{0x10040400} & \texttt{0x10040402} & OK \\
    \\
    \textbf{\texttt{TIM10}} \\
    \texttt{CR1}  & \texttt{0x81} & \texttt{0x80} & \texttt{CEN} not set! \\
    \texttt{SR}   & \texttt{0x3} & \texttt{0x1} & No interrupt flag \\
    \texttt{CNT}  & \texttt{0x6c3} & \texttt{0x0} & Not running! \\
    \texttt{CCR1} & \texttt{0x2a30} & \texttt{0x1518} & OK
  \end{tabular}
\end{center}

\end{document}

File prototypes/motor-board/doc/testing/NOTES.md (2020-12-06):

# Initial tests driving motor prototype board from AD2

Setup:

 - Connect 5V power supply to motor board [DONE]

 - Connect 3.3V supply from AD2 to motor board [DONE]

 - Configure two AD2 digital outputs for `MOTOR_IN1` and `MOTOR_IN2` [DONE]

 - Configure AD2 digital input for `PULSE` [DONE]

 - Configure AD2 analog input for `MOTOR_SENSE` [DONE]

Protocol:
  1. Remove 5V power from motor board
  2. Disconnect `MOTOR_IN1` and `MOTOR_IN2` from motor board
  3. Configure AD2 digital outputs in "Patterns" panel and check
  4. Connect `MOTOR_IN1` and `MOTOR_IN2` to motor board
  5. Apply 5V power to motor board
  6. Run AD2 digital output waveform generator
  7. Record results: motor motion, `PULSE` and `MOTOR_SENSE` inputs

Experiments:

    STATE          MOTOR_IN1      MOTOR_IN2

    Motor halted   HIGH           HIGH
    Forward 10%    HIGH           PWM: 10% LOW
    Forward 50%    HIGH           PWM: 50% LOW
    Forward 100%   HIGH           LOW
    Backward 10%   PWM: 10% LOW   HIGH
    Backward 50%   PWM: 50% LOW   HIGH
    Backward 100%  LOW            HIGH

=> ALL WORKS! DIDN'T BOTHER WITH PROTOCOL ABOVE, JUST SWITCHING PWM
   FREQUENCIES IN PATTERNS OUTPUT. PERFECT RESULTS, AS FAR AS I CAN
   TELL. ONLY THING THAT WILL NEED A LITTLE WORK IS SMOOTHING OF PULSE
   TIMES FROM ENCODER, BECAUSE THE ENCODER DISK ISN'T QUITE STRAIGHT.
   BUT: PWM SPEED CONTROL WORKS, FORWARDS AND BACKWARDS; PULSE OUTPUT
   FROM ENCODER WORKS; TORQUE MEASUREMENT WORKS!

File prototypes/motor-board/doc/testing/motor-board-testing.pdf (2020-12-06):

## Mini-Mapper motor prototype board testing

Ian Ross

December 6, 2020

This document reports testing of the motor prototype board:

1. Basic tests of the electronics by driving the PWM inputs on the board using the Analog Discovery 2, and using the logic analyser and scope functions of the AD2 to monitor the motor encoder and torque measurement outputs.
2. Tests of the software running on the STM32F767ZI Nucleo-144 board, connected to the Analog Discovery 2 to monitor PWM outputs and provide synthetic inputs for the motor encoder and torque measurement code.
3. “Live” testing of the software, connecting the motor board to the Nucleo-144 board.

The software used for these tests is the shell-motor application, which provides a command line interface for basic motor operations. (Once this is all working, the emphasis will shift to using a Python test bench GUI on a PC to talk to driver code on the Nucleo board.)

## 1 Motor board initial testing

Setup

The motor board and AD2 are set up as follows for this series of tests:

- Connect 5V wall wart power supply to motor board.
- Connect 3.3V supply from AD2 to motor board.
- Configure two AD2 digital outputs for MOTOR_IN1 and MOTOR_IN2.
- Configure AD2 digital input for PULSE.
- Configure AD2 analog input for MOTOR_SENSE.

The initial protocol for testing here was something like this:

1. Remove 5V power from motor board.

1

2. Disconnect MOTOR_IN1 and MOTOR_IN2 from motor board.
3. Configure AD2 digital outputs in “Patterns” panel and check.
4. Connect MOTOR_IN1 and MOTOR_IN2 to motor board.
5. Apply 5V power to motor board.
6. Run AD2 digital output waveform generator.
7. Record results: motor motion, PULSE and MOTOR_SENSE inputs.

The control states I tested with this setup were:

State | MOTOR_IN1 | MOTOR_IN2
Motor halted | HIGH | HIGH
Forward 10% | HIGH | PWM: 10% LOW
Forward 50% | HIGH | PWM: 50% LOW
Forward 100% | HIGH | LOW
Backward 10% | PWM: 10% LOW | HIGH
Backward 50% | PWM: 50% LOW | HIGH
Backward 100% | LOW | HIGH

Results

- Quite shockingly, everything worked first time!
- After the initial setup, I didn’t bother too much with the protocol above, just switching the PWM duty cycle in the AD2 “Patterns” panel. (Which is a more realistic test than I was originally planning to do anyway.)
- The results were pretty much perfect, as far as I can tell. There are only two things that might need some attention.
- Pulse times from the motor encoder might need some smoothing, because the encoder disk isn’t quite straight.
- The signal from the motor coil current sense amplifier that I’m going to use for torque measurements is quite noisy, but that may just be due to seeing the PWM switching frequency coming through into the motor coil current.
- But: PWM speed control works, forwards and backwards; the pulse output from the motor encoder works; and torque measurement “works”, though I need to figure out exactly what I’m seeing there.

A better solution for the wobble in the motor encoder signal is probably to correct the mounting of the encoder disk to the motor shaft. I designed the hole in the encoder disk under-size to ensure a tight fit, but it’s too tight because the

| 2

encoder disks are manufactured as PCBs and have two layers of copper with no relief around the mounting hole. That means that it’s not possible to push the encoder disk onto the motor shaft without expanding the hole in the disk. I did that in a not very careful way for the disk I’m currently using, but I have two others, and could try to drill an accurate 2 mm hole in them to fit exactly the diameter of the motor shaft (and then glue them in place).
As for what’s going on with the motor coil current signal, I need to investigate that in more detail, but there is at least something reasonable there, and the DC level of the signal does go up and down as the motor drive PWM duty cycle is set to higher and lower values.

## 2 Software testing

Setup

The Nucleo board and AD2 are set up as follows for this series of tests:

- Connect ground between Nucleo board and AD2.
- Connect PE5 and PE6 on Nucleo (MOTOR_IN1 and MOTOR_IN2 motor PWM outputs) to logic pins 0 and 1 (inputs) on the AD2.
- Connect PB10 on Nucleo (PULSE motor encoder input) to logic pin 2 (output) on AD2.
- Connect PA4 on Nucleo (MOTOR_SENSE analogue torque input) to AD2 analogue waveform output W1.

The idea here is for the software on the Nucleo board to drive the PWM motor driver signals and for these to be observed by the AD2’s logic analyser. The motor encoder input to the Nucleo board will be driven by the AD2’s pattern generator, and the analogue torque input to the Nucleo board will be driven by the AD2’s signal generator.
The AD2 Waveforms software should be configured as follows:
- Logic analyser with inputs 1 and 2 for motor PWM signals from Nucleo board.
- Pattern generator to logic pin 3 for variable frequency square wave to drive motor encode input on Nucleo board.
- Signal generator to output W1 to drive motor torque measurement input on Nucleo board.

Test command script:

3

# Ensure initial state and command processing OK.

stop

# Test basic motor commanding.

forward 10
stop
reverse 10
stop

# Test torque measurement.

torque on

# Modify DC level of analogue output from AD2 signal generator to test # different motor coil current levels.

set torque-interval 5000
set torque-interval 500
torque off

# Test motor speed encoder.

encoder on

# Modify frequency of square wave output from AD2 pattern generator to # test different motor speed measurements.

set encoder-interval 5000
set encoder-interval 500
encoder off

Results

- stop gives: DIO0 low, DIO1 high. (WRONG: should be both high.)
- forward 10 gives: DIO0 high, DIO1 high. (WRONG: should be both DIO0 high, DIO1 PWM.)
- reverse 10 gives: DIO0 PWM, DIO1 high. (WRONG: should be both high.)

4

### 2.1 PWM shell regression testing

Register | Old: works | New: broken | Status
RCC
AHB1ENR | 0x30000a | 0x30000f | OK
APB1ENR | 0x10040400 | 0x10040402 | OK

TIM10
CR1 | 0x81 | 0x80 | CEN not set!
SR | 0x3 | 0x1 | No interrupt flag
CNT | 0x6c3 | 0x0 | Not running!
CCR1 | 0x2a30 | 0x1518 | OK

5

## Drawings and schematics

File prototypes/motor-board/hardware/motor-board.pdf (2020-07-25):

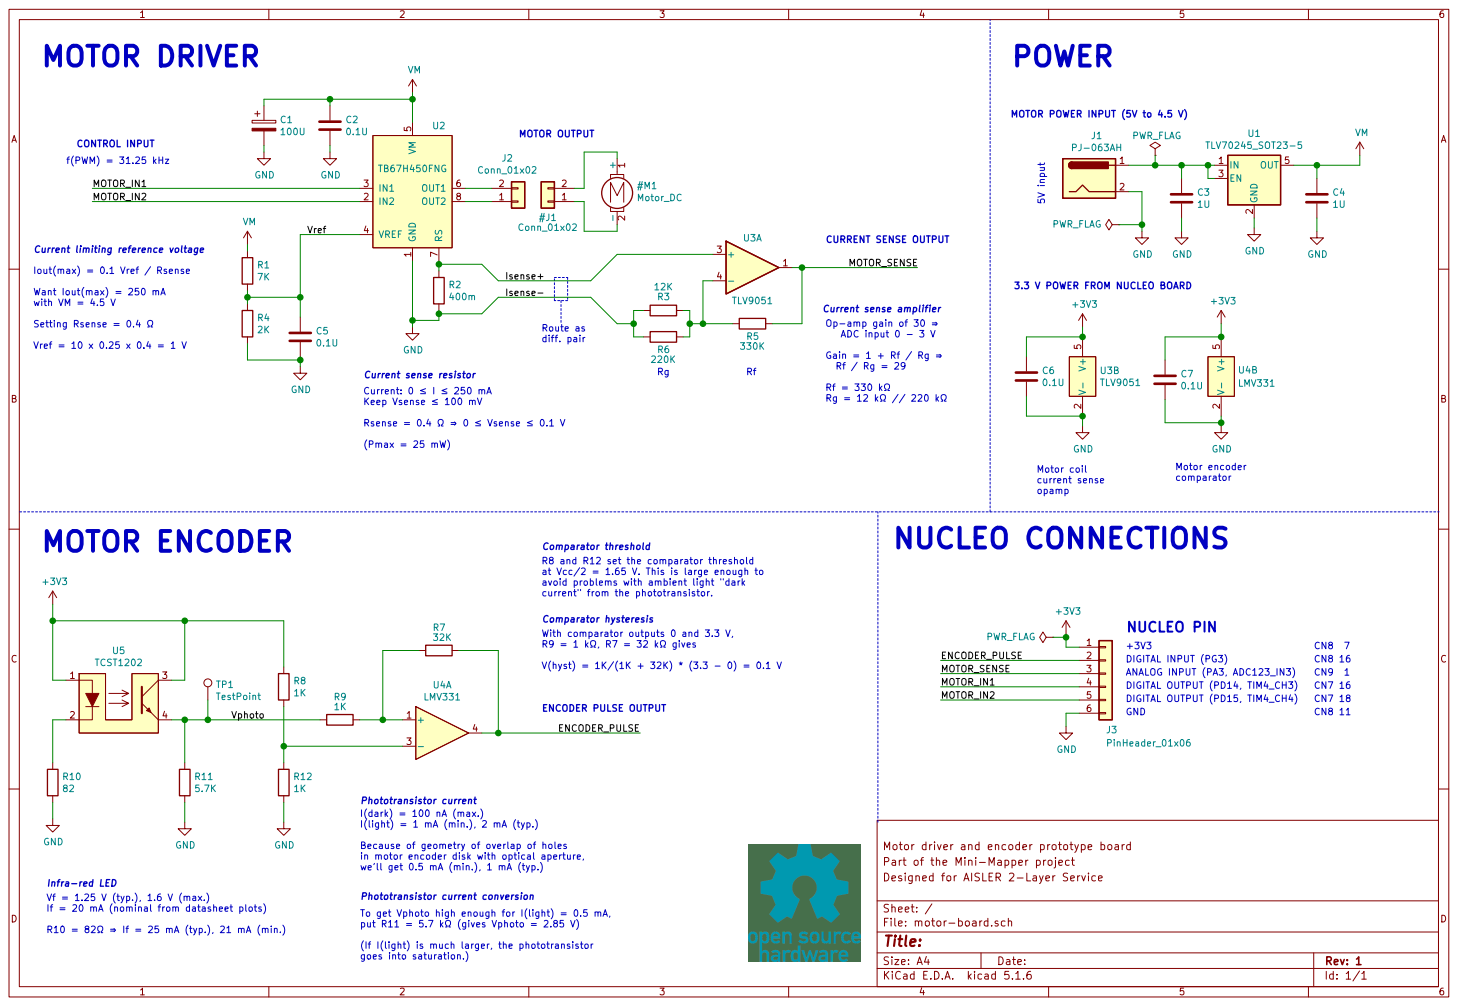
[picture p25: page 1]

MOTOR POWER INPUT (5V to 4.5 V)

Route as diff. pair Phototransistor current

Rf / Rg = 29 Rf = 330 k Rg = 12 k // 220 k MOTOR OUTPUT

2 EN 3 OUT 5 U1 TLV70245_SOT23-5 GND GND
PWR_FLAG

Motor driver and encoder prototype board V- 2 V+

NUCLEO CONNECTIONS 5V input Motor coil current sense

Iout(max) = 0.1 Vref / Rsense
3.3 V POWER FROM NUCLEO BOARD MOTOR ENCODER
Want Iout(max) = 250 mA with VM = 4.5 V
+3V3 GND

Keep Vsense 100 mV Rsense = 0.4 0 Vsense 0.1 V

Comparator threshold
R8 and R12 set the comparator threshold
at Vcc/2 = 1.65 V. This is large enough to
avoid problems with ambient light "dark
current" from the phototransistor.

Comparator hysteresis Phototransistor current conversion

With comparator outputs 0 and 3.3 V,
R9 = 1 k, R7 = 32 k gives

I(dark) = 100 nA (max.)
I(light) = 1 mA (min.), 2 mA (typ.)

Because of geometry of overlap of holes
in motor encoder disk with optical aperture,
we'll get 0.5 mA (min.), 1 mA (typ.)

Part of the Mini-Mapper project
Id: 1/1 Title: File: motor-board.sch Sheet: / Designed for AISLER 2-Layer Service

If = 20 mA (nominal from datasheet plots)

To get Vphoto high enough for I(light) = 0.5 mA,
put R11 = 5.7 k (gives Vphoto = 2.85 V)

R10 = 82 If = 25 mA (typ.), 21 mA (min.)

(If I(light) is much larger, the phototransistor
goes into saturation.)

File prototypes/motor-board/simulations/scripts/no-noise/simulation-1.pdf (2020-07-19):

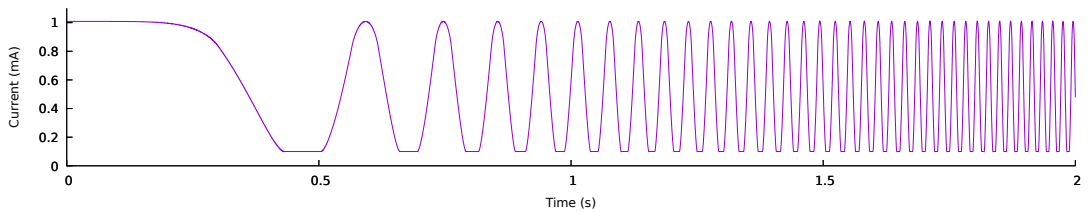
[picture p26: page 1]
Current (mA); Time (s)

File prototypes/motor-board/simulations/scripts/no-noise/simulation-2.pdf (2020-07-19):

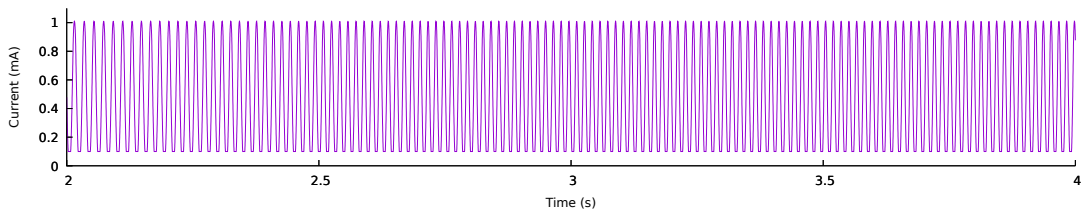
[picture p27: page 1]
Current (mA); Time (s)

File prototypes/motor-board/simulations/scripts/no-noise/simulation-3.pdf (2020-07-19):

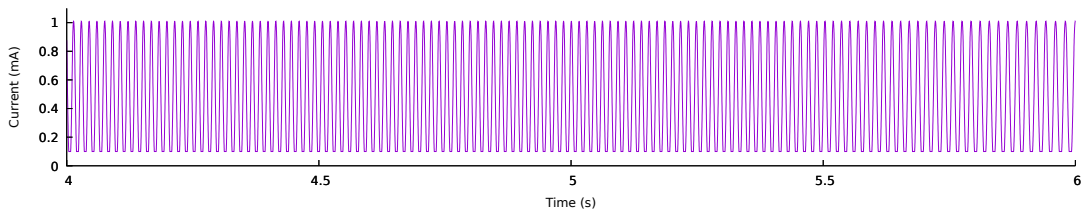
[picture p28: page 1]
Current (mA); Time (s)

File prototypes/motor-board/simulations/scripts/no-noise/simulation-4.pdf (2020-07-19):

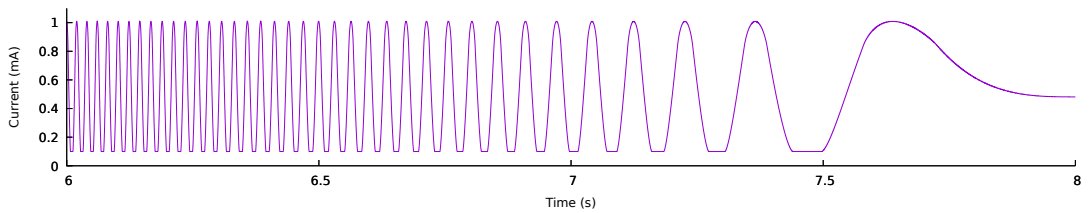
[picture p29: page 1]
Current (mA); Time (s)

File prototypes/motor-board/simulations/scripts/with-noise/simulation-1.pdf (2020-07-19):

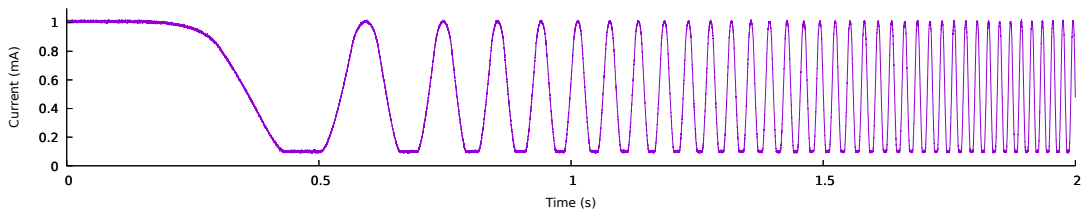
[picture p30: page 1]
Current (mA); Time (s)

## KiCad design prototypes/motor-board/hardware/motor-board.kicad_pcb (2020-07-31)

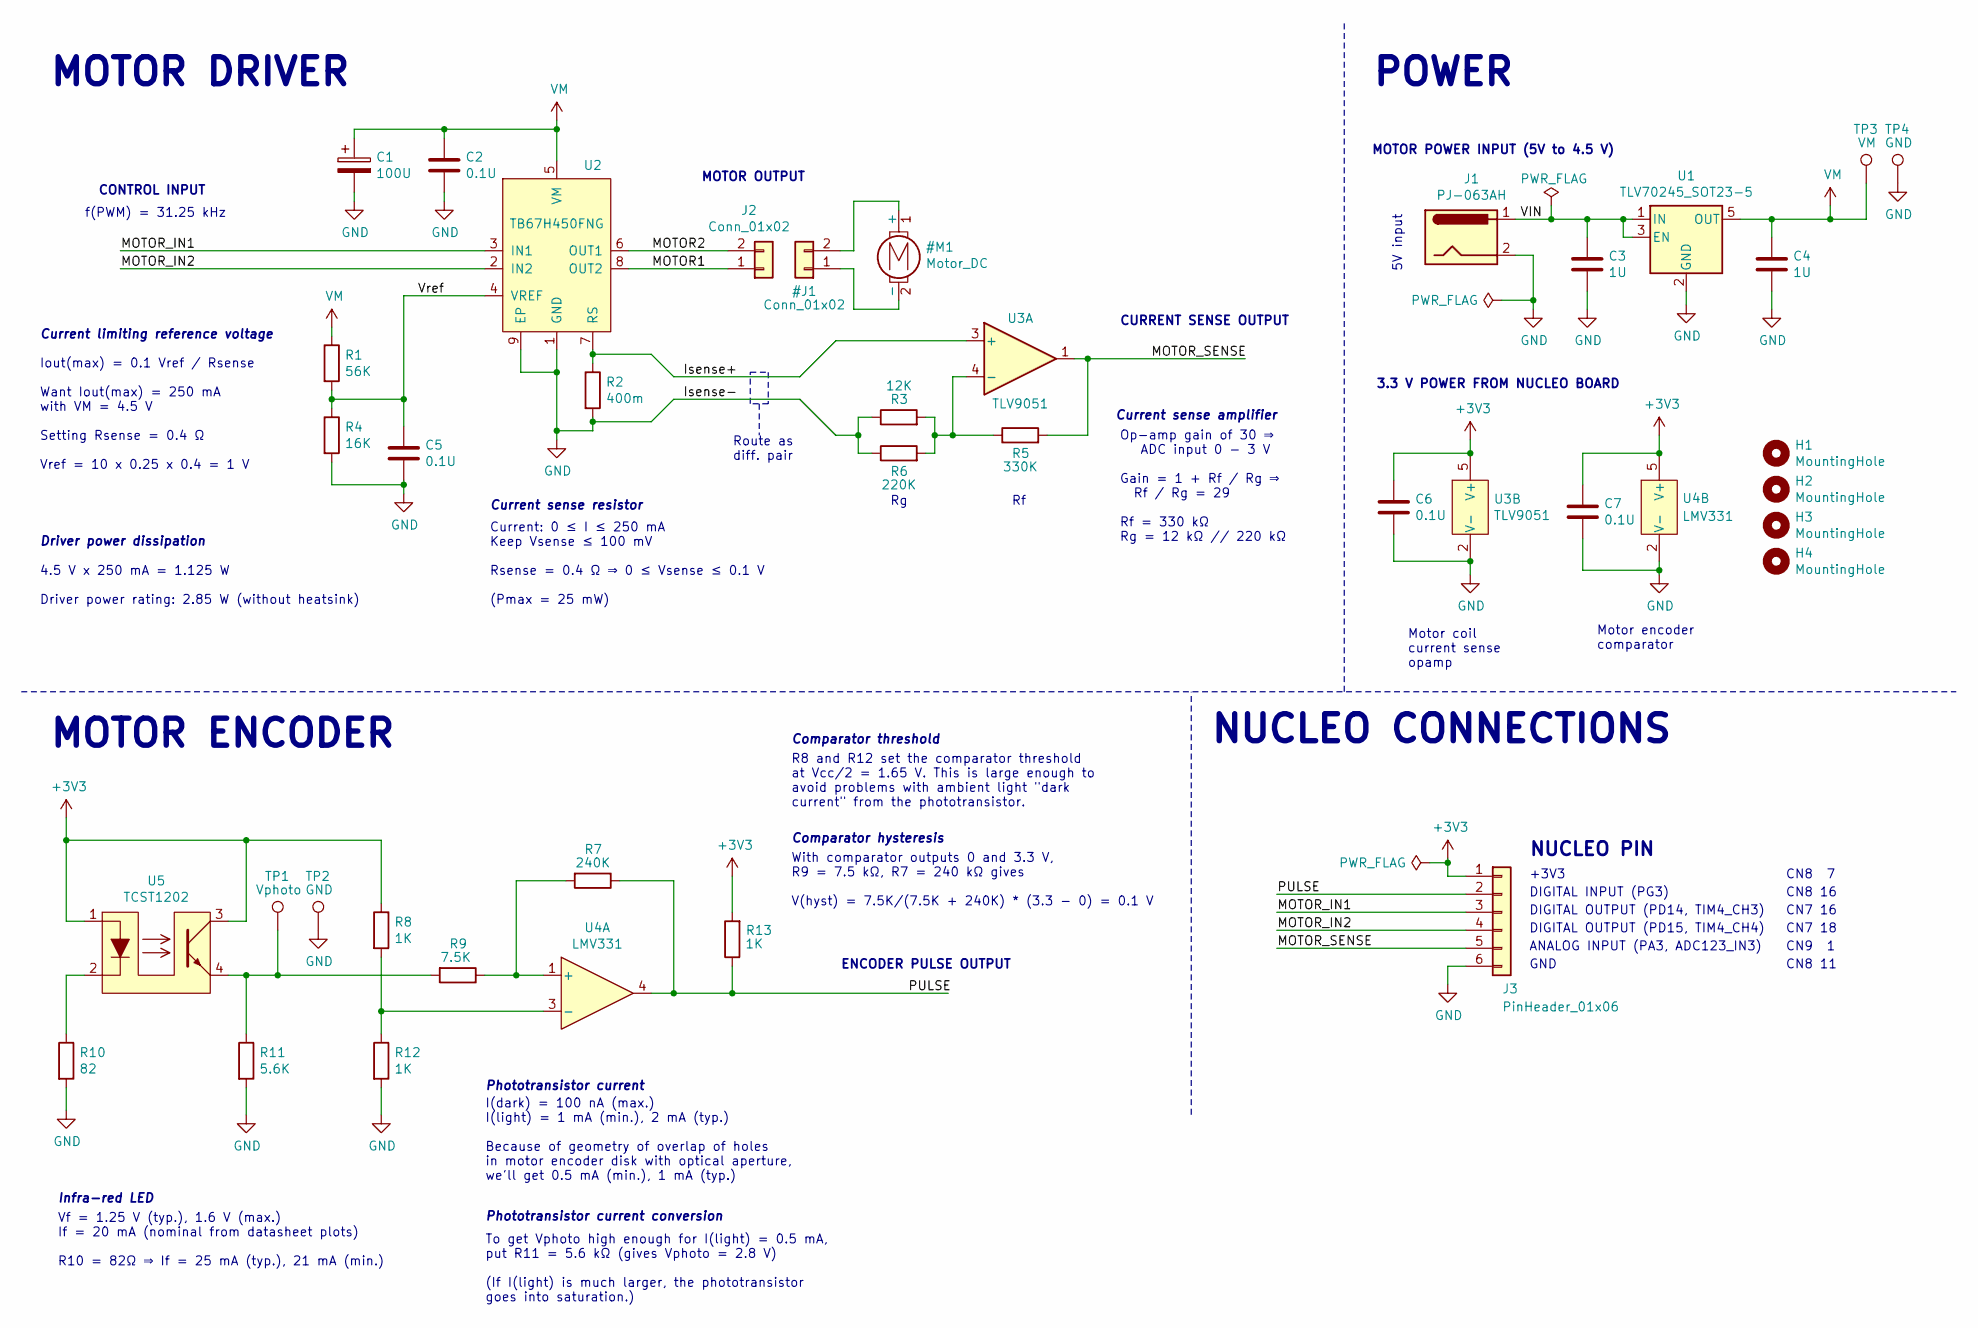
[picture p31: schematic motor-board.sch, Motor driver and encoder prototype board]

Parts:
C1: 100U; CP_Elec_6.3x7.7; MPN EEE-HC1C101XP
C2, C5, C6, C7: 0.1U; C_0805; MPN 885012207098
C3, C4: 1U; C_0805; MPN 885012107015
H1, H2, H3, H4: MountingHole; MountingHole_2.7mm_M2.5; MPN n/a
J1: PJ-063AH; BarrelJack_CUI_PJ-063AH_Horizontal; MPN PJ-063AH
J2: Conn_01x02; PinSocket_1x02_P2.54mm_Vertical; MPN SLW-102-01-T-S
J3: PinHeader_01x06; PinHeader_1x06_P2.54mm_Vertical; MPN 22-28-4060
R1: 56K; R_0805; MPN CRGP0805F56K
R2: 400m; R_0805; MPN RL0805FR-070R4L
R3: 12K; R_0805; MPN CRCW080512K0FKEA
R4: 16K; R_0805; MPN CRCW080516K0FKEA
R5: 330K; R_0805; MPN CRCW0805330KFKEA
R6: 220K; R_0805; MPN CRGP0805F220K
R7: 240K; R_0805; MPN CRCW0805240KFKEA
R8, R12: 1K; R_0805; MPN CRGP0805F1K0
R9: 7.5K; R_0805; MPN CRCW08057K50FKEA
R10: 82; R_0805; MPN CRCW080582R0FKEA
R11: 5.6K; R_0805; MPN CRCW08055K60FKEAC
R13: 1K; R_0805; MPN CRCW0805240KFKEA
TP1: Vphoto; TestPoint_Pad_2.0x2.0mm; MPN n/a
TP2, TP4: GND; TestPoint_Pad_2.0x2.0mm; MPN n/a
TP3: VM; TestPoint_Pad_2.0x2.0mm; MPN n/a
U1: TLV70245_SOT23-5; SOT-23-5; MPN TLV70245DBVR
U2: TB67H450FNG; SOIC127P600X175-9N; MPN TB67H450FNG
U3: TLV9051; SOT-23-5; MPN TLV9051IDBVR
U4: LMV331; SOT-23-5; MPN LMV331IDBVR
U5: TCST1202; MPN TCST1202

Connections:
+3V3: C6.1, C7.1, J3.1, R8.1, R13.2, U3.5 (V+), U4.5 (V+), U5.1, U5.3
/Isense+: R2.1, U2.7 (RS), U3.3 (+)
/MOTOR1: J2.1, U2.8 (OUT2)
/MOTOR2: J2.2, U2.6 (OUT1)
/MOTOR_IN1: J3.3, U2.3 (IN1)
/MOTOR_IN2: J3.4, U2.2 (IN2)
/MOTOR_SENSE: J3.5, R5.2, U3.1
/PULSE: J3.2, R7.1, R13.1, U4.4
/VIN: C3.1, J1.1, U1.1 (IN), U1.3 (EN)
/Vref: C5.1, R1.2, R4.1, U2.4 (VREF)
GND: C1.2, C2.2, C3.2, C4.2, C5.2, C6.2, C7.2, J1.2, J3.6, R2.2, R3.1, R4.2, R6.1, R10.2, R11.2, R12.2, TP2.1, TP4.1, U1.2 (GND), U2.1 (GND), U2.9 (EP), U3.2 (V-), U4.2 (V-)
unnamed: R3.2, R5.1, R6.2, U3.4 (-)
unnamed: R7.2, R9.1, U4.1 (+)
unnamed: R10.1, U5.2
unnamed: R9.2, R11.1, TP1.1, U5.4
unnamed: R8.2, R12.1, U4.3 (-)
VM: C1.1, C2.1, C4.1, R1.1, TP3.1, U1.5 (OUT), U2.5 (VM)

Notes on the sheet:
Current sense resistor
Current limiting reference voltage
MOTOR OUTPUT
Op-amp gain of 30 ⇒ ADC input 0 - 3 V Gain = 1 + Rf / Rg ⇒ Rf / Rg = 29 Rf = 330 kΩ Rg = 12 kΩ // 220 kΩ
MOTOR POWER INPUT (5V to 4.5 V)
CONTROL INPUT
CURRENT SENSE OUTPUT
Current: 0 ≤ I ≤ 250 mA Keep Vsense ≤ 100 mV Rsense = 0.4 Ω ⇒ 0 ≤ Vsense ≤ 0.1 V (Pmax = 25 mW)
Iout(max) = 0.1 Vref / Rsense Want Iout(max) = 250 mA with VM = 4.5 V Setting Rsense = 0.4 Ω Vref = 10 x 0.25 x 0.4 = 1 V
Route as diff. pair
Current sense amplifier
MOTOR DRIVER
MOTOR ENCODER
ENCODER PULSE OUTPUT
Vf = 1.25 V (typ.), 1.6 V (max.) If = 20 mA (nominal from datasheet plots) R10 = 82Ω ⇒ If = 25 mA (typ.), 21 mA (min.)
3.3 V POWER FROM NUCLEO BOARD
Motor coil current sense opamp
Motor encoder comparator
I(dark) = 100 nA (max.) I(light) = 1 mA (min.), 2 mA (typ.) Because of geometry of overlap of holes in motor encoder disk with optical aperture, we'll get 0.5 mA (min.), 1 mA (typ.)
Infra-red LED
Phototransistor current
To get Vphoto high enough for I(light) = 0.5 mA, put R11 = 5.6 kΩ (gives Vphoto = 2.8 V) (If I(light) is much larger, the phototransistor goes into saturation.)
Phototransistor current conversion
Comparator hysteresis
With comparator outputs 0 and 3.3 V, R9 = 7.5 kΩ, R7 = 240 kΩ gives V(hyst) = 7.5K/(7.5K + 240K) * (3.3 - 0) = 0.1 V
Comparator threshold
R8 and R12 set the comparator threshold at Vcc/2 = 1.65 V. This is large enough to avoid problems with ambient light "dark current" from the phototransistor.
POWER
5V input
NUCLEO CONNECTIONS
+3V3
GND
DIGITAL OUTPUT (PD14, TIM4_CH3)
DIGITAL OUTPUT (PD15, TIM4_CH4)
ANALOG INPUT (PA3, ADC123_IN3)
DIGITAL INPUT (PG3)
NUCLEO PIN
CN8 7
CN8 11
CN7 16

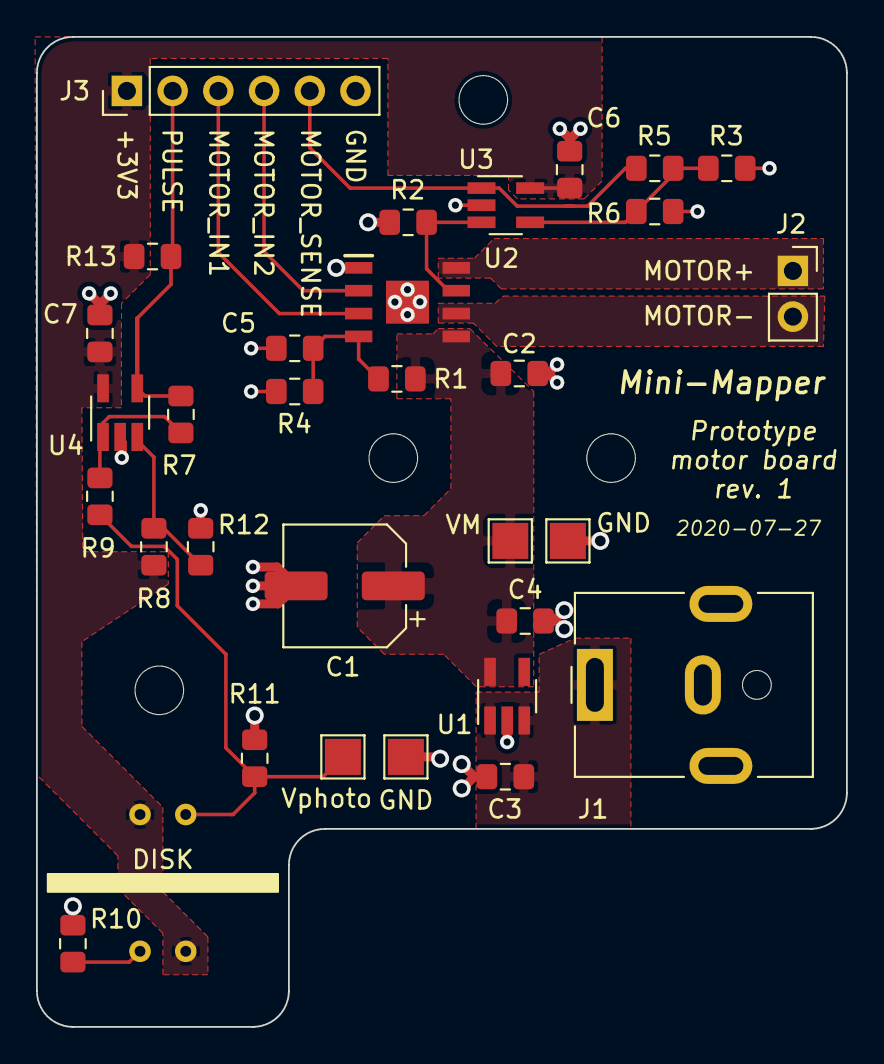
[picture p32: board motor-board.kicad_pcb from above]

Board: 2 copper layers, 45.0 x 55.0 mm, 36 parts (1 on the bottom side), 17 nets.

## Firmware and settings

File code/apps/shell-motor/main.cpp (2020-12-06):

// Command shell with motor and LED blinky modules.

#include <cstring>

// Hardware includes: Nucleo board BSP and setup functions.
#include "bsp-nucleo.h"
#include "setup.hpp"

// Library includes.
#include "events.hpp"
#include "pin.hpp"
#include "usart.hpp"
#include "terminal.hpp"
#include "shell.hpp"

// Shell modules.
#include "blinky_module.hpp"
#include "motor_module.hpp"


// Event management for real hardware plus setup for terminal using
// USART3 (which is connected to the ST-Link debugger on the
// STM32F767ZI Nucleo board).

inline void wfe(void) { __WFE(); }
Events::Manager ev(wfe);

using Terminal = TerminalT<USART>;
USART usart3(3, PD8, GPIO_AF_7, PD9, GPIO_AF_7, DMAChannel { 1, 3, 4 });
Terminal terminal(usart3);

BlinkyModule blinky;
MotorModule motor;

extern "C" void USART3_IRQHandler(void) { usart3.rx_irq(); }
extern "C" void DMA1_Stream3_IRQHandler(void) { usart3.tx_dma_irq(); }
extern "C" void SysTick_Handler(void) { ev.post(Events::SYSTICK); }
extern "C" void DMA2_Stream0_IRQHandler(void) { motor.torque_dma_irq(); }
extern "C" void TIM2_IRQHandler(void) { motor.encoder_irq(); }

int main(void)
{
  // Standard cache and clock setup, set SysTick to 1 kHz, set
  // terminal to interactive (which gives prompts and rudimentary line
  // editing).
  enable_caches();
  configure_clock();
  SysTick_Config(SystemCoreClock / 1000);
  terminal.set_interactive(true);
  motor.init();

  // Create command shell with core module (which implements the "set"
  // and "show" commands) and motor and LED blinky modules.
  Shell::CommandShell shell(terminal);
  shell += motor;
  shell += blinky;

  // Add all event consumers to event manager.
  ev += usart3;
  ev += terminal;
  ev += shell;
  ev += blinky;
  ev += motor;
  ev += motor.motor_encoder();

  ev.loop();
}

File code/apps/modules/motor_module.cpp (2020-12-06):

#include <cctype>
#include <cstring>
#include <math.h>

#include "motor_module.hpp"
#include "motor-controller.hpp"
#include "terminal.hpp"

using Terminal = TerminalT<USART>;
extern Terminal terminal;


static bool parse_int(const char *s, int &val);
static void print_frac(float x);

MotorModule::MotorModule() :
  Shell::Module{"motor"}, Events::Consumer{"MotorModule"},
  // TODO: FIX THIS
  torque_cal{},
  torque_dma{2, 0, 0},
  torque{TIM4, ADC1, torque_dma, 100, torque_cal, PA4, PA5},
  wheel_info{
    .circumference = static_cast<uint32_t>(60.0 * M_PI * 1000.0),
    .encoder_gear_ratio = 48,
    .encoder_teeth = 12
  },
  encoder{TIM2, PB10, PB11, wheel_info},
  controller{Motor::LEFT, torque, encoder, TIM9, 30000, PE5, PE6} { }


// Event dispatching just uses SysTick events to report values from
// the torque measurement and position encoder.

void MotorModule::dispatch(const Events::Event &e) {
  if (e.tag != Events::SYSTICK)
    return;

  if (torque_display_interval > 0 &&
      ++torque_display_ticks == torque_display_interval) {
    torque_display_ticks = 0;
    terminal.print("TORQUE: ADC=");
    print_frac(torque.adc_count(Motor::Torque::SMOOTHED, Motor::LEFT));
    terminal.print("  =>  ");
    print_frac(1000 * torque.current(Motor::Torque::SMOOTHED, Motor::LEFT));
    terminal.println(" mA");
  }

  if (encoder_display_interval > 0 &&
      ++encoder_display_ticks == encoder_display_interval) {
    encoder_display_ticks = 0;
    torque_display_ticks = 0;
    terminal.print("ENCODER: INT=");
    print_frac(encoder.interval(Motor::Encoder::BOXCAR, Motor::LEFT));
    terminal.print(" us   SPEED=");
    print_frac(1000 * encoder.speed(Motor::Encoder::BOXCAR, Motor::LEFT));
    terminal.println(" mm/s");
  }
}

static void print_frac(float x) {
  terminal.print(static_cast<int>(x));
  terminal.print(".");
  int frac = static_cast<int>(x * 100) - static_cast<int>(x) * 100;
  if (frac == 0) terminal.print("00");
  else if (frac < 10) {
    terminal.print("0");
    terminal.print(frac);
  } else
    terminal.print(frac);
}


Shell::CommandResult
MotorModule::set_variable(const char *name, const char *value) {
  int val;
  if (!strcmp(name, "torque-interval")) {
    if (!parse_int(value, val))
      return Shell::INVALID_VALUE_FOR_VARIABLE;
    torque_display_interval_var = val;
    if (torque_display_interval >= 0) {
      torque_display_interval = val;
      torque_display_ticks = 0;
    }
    return Shell::COMMAND_OK;
  } else if (!strcmp(name, "encoder-interval")) {
    if (!parse_int(value, val))
      return Shell::INVALID_VALUE_FOR_VARIABLE;
    if (encoder_display_interval >= 0) {
      encoder_display_interval_var = val;
      encoder_display_ticks = 0;
    }
    return Shell::COMMAND_OK;
  }
  return Shell::SKIPPED;
}

Shell::CommandResult MotorModule::show_variable(const char *name) {
  if (!strcmp(name, "torque-interval")) {
    terminal.println(torque_display_interval_var);
    return Shell::COMMAND_OK;
  } else if (!strcmp(name, "encoder-interval")) {
    terminal.println(encoder_display_interval_var);
    return Shell::COMMAND_OK;
  }
  return Shell::SKIPPED;
}


// Commands:
//  - stop
//  - forward <pwm-duty-pct>
//  - reverse <pwm-duty-pct>
//  - torque on|off
//  - encoder on|off

Shell::CommandResult MotorModule::run_command
  (const char *cmd, int nargs, char *args[]) {
  if (!strcmp(cmd, "stop") && nargs == 0) {
    controller.stop();
    terminal.println("STOPPED");
    return Shell::COMMAND_OK;
  } else if (!strcmp(cmd, "forward") && nargs == 1) {
    int val;
    if (!parse_int(args[0], val))
      return Shell::COMMAND_PARAMETER_ERROR;
    if (val > 100) val = 100;
    controller.forward(val);
    return Shell::COMMAND_OK;
  } else if (!strcmp(cmd, "reverse") && nargs == 1) {
    int val;
    if (!parse_int(args[0], val))
      return Shell::COMMAND_PARAMETER_ERROR;
    if (val > 100) val = 100;
    controller.reverse(val);
    return Shell::COMMAND_OK;
  } else if (!strcmp(cmd, "torque") && nargs == 1) {
    if (!strcmp(args[0], "on")) {
      torque_display_interval = torque_display_interval_var;
      torque_display_ticks = 0;
      controller.measure_torque(true);
      return Shell::COMMAND_OK;
    } else if (!strcmp(args[0], "off")) {
      torque_display_interval = -1;
      return Shell::COMMAND_OK;
    }
    return Shell::COMMAND_PARAMETER_ERROR;
  } else if (!strcmp(cmd, "encoder") && nargs == 1) {
    if (!strcmp(args[0], "on")) {
      encoder_display_interval = encoder_display_interval_var;
      encoder_display_ticks = 0;
      controller.measure_torque(false);
      return Shell::COMMAND_OK;
    } else if (!strcmp(args[0], "off")) {
      encoder_display_interval = -1;
      return Shell::COMMAND_OK;
    }
    return Shell::COMMAND_PARAMETER_ERROR;
  }
  return Shell::SKIPPED;
}


// Parse PWM duty cycle values from strings.

static bool parse_int(const char *s, int &val) {
  for (val = 0; *s != '\0' && isdigit(*s); ++s) {
    val = val * 10 + *s - '0';
  }
  return *s == '\0';
}

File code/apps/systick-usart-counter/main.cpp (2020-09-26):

// Simple SysTick-driven USART demonstration.

// Hardware includes: Nucleo board BSP and setup functions.
#include "bsp-nucleo.h"
#include "setup.hpp"

// Library includes.
#include "events.hpp"
#include "pin.hpp"
#include "usart.hpp"


inline void wfe(void) { __WFE(); }
Events::Manager ev(wfe);


USART usart3(3, PD8, GPIO_AF_7, PD9, GPIO_AF_7, DMAChannel { 1, 3, 4 });

extern "C" void USART3_IRQHandler(void) { usart3.rx_irq(); }
extern "C" void DMA1_Stream3_IRQHandler(void) { usart3.tx_dma_irq(); }
extern "C" void SysTick_Handler(void) { ev.post(Events::SYSTICK); }


// Write a message to USART every second (measured by SysTick), and
// write additional messages echoing characters received on USART.

class TickerWriter : public Events::Consumer {
public:

  TickerWriter() : Events::Consumer("TickerWriter") { }

  // Event dispatch...
  void dispatch(const Events::Event &e) {
    switch (e.tag) {
    case Events::SYSTICK:
      if (++tick_counter == 1000) {
        tick_counter = 0;
        write_tick_message(count++);
      }
      break;

    case Events::USART_RX_CHAR:
      write_rx_message(e.param);
      break;

    default:
      break;
    }
  }

private:

  void write_tick_message(int c);
  void write_rx_message(char c);

  int tick_counter = 0;
  int count = 0;
};

const int MAX_DIGITS = 16;
char buff[MAX_DIGITS + 1];

void TickerWriter::write_tick_message(int c) {
  for (auto ch: "TICK: ") usart3.tx(ch);
  buff[MAX_DIGITS] = '\0';
  int idx = MAX_DIGITS;
  do {
    buff[--idx] = '0' + c % 10;
    c /= 10;
  } while (c > 0);
  while (buff[idx])
    usart3.tx(buff[idx++]);
  for (auto ch: "\r\n") usart3.tx(ch);
  usart3.flush();
}

void TickerWriter::write_rx_message(char c) {
  for (auto ch: "RX: '") usart3.tx(ch);
  usart3.tx(c);
  for (auto ch: "'\r\n") usart3.tx(ch);
  usart3.flush();
}

TickerWriter ticker;

int main(void)
{
  enable_caches();
  configure_clock();
  SysTick_Config(SystemCoreClock / 1000);

  ev += ticker;
  ev += usart3;
  ev.loop();
}

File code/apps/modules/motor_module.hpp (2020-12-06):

#ifndef _H_MOTOR_MODULE_
#define _H_MOTOR_MODULE_

#include "bsp-nucleo.h"

#include "pin.hpp"
#include "dma.hpp"
#include "shell.hpp"
#include "motor-torque.hpp"
#include "motor-encoder.hpp"
#include "motor-controller.hpp"


// Shell module to control MOTOR driver.

class MotorModule : public Shell::Module, public Events::Consumer {
public:

  MotorModule();
  void init(void) override { controller.init(); }

  // Event dispatch (from Events::Consumer).
  void dispatch(const Events::Event &e) override;

  // Shell command and variable processing (from Shell::Module).
  Shell::CommandResult set_variable(const char *name, const char *value) override;
  Shell::CommandResult show_variable(const char *name) override;
  Shell::CommandResult run_command(const char *cmd, int nargs, char *args[]) override;

  // Called from ISR for torque DMA stream.
  void torque_dma_irq(void) { torque.dma_transfer_complete_irq(); }

  // Called from ISR for encoder timer capture.
  void encoder_irq(void) { encoder.timer_capture_irq(); }

  Motor::Encoder &motor_encoder(void) { return encoder; }

private:

  Motor::Torque::Calibration torque_cal;
  DMAChannel torque_dma;
  Motor::Torque torque;
  Motor::Encoder::WheelInfo wheel_info;
  Motor::Encoder encoder;
  Motor::Controller controller;

  int torque_display_ticks;
  int torque_display_interval = -1;
  int torque_display_interval_var = 1000;
  int encoder_display_ticks;
  int encoder_display_interval = -1;
  int encoder_display_interval_var = 1000;
};

#endif

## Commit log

2020-06-26 Motor driver comparison; KiCad setup; start motor board schematic
    [motor-board.kicad_pcb, motor-board.sch, motor-driver-comparison.ods]
2020-06-28 MCAD for chassis and motor
    [chassis-plate.FCStd, motor-encoder-disk.FCStd, motor.FCStd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]
2020-06-28 Fix corrupted KiCad symbol library metadata
2020-07-01 Correct sense resistor value
    [motor-board.sch]
2020-07-01 Add some footprints to library symbols
    [motor-board.sch]
2020-07-03 Add some more footprints; set up link field for symbols
    [motor-board.sch]
2020-07-05 More mechanical models
    [castor.FCStd, chassis-plate.FCStd, motor-mount-bracket.FCStd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]
2020-07-08 Mechanical modelling for motor encoder setup
    [motor-proto-pcb.FCStd, pcb-standoff.FCStd, photo-interrupter.FCStd]
2020-07-08 Small improvements to motor prototype schematic
    - Move motor off board
    - Set up to route current sensing connection as differential pair
    [motor-board.sch]
2020-07-11 Moved some thing around; photointerrupter signal calculation
    [motor-board.kicad_pcb, motor-board.sch, motor-driver-comparison.ods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]
2020-07-12 More MCAD; photointerrupter comparison spreadsheet
    [chassis-plate.FCStd, motor.FCStd, photointerrupter-comparison.ods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]
2020-07-19 More work on motor encoder; KiCad library reorganisation
    [chassis-plate.FCStd, motor-board.sch, pcb-standoff-3mm.FCStd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]
2020-07-19 Motor encoder comparator setup
    [motor-board.sch]
2020-07-22 Tidy up motor encoder; simulations; start on power
2020-07-22 More on simulations; motor board power
    [motor-board.sch]
2020-07-23 Motor board schematic close to complete
    [chassis-plate.FCStd, motor-board.sch, motor-mount-bracket.FCStd]
2020-07-25 Finish up motor board schematic; start on layout
    [motor-board.kicad_pcb, motor-board.sch]
2020-07-27 Finished layout; checklists
    [mechanical-interface.FCStd, mechanical-interface.dxf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]
2020-07-27 Missed some changes...
    [motor-board.kicad_pcb, motor-board.sch]
2020-07-28 Finalise motor board layout; schematic and layout checklist
    [motor-board-bom.ods, motor-board.kicad_pcb, motor-board.sch]
2020-07-28 Updated BOM spreadsheet
    [motor-board-bom.ods]
2020-07-29 Motor prototype setup CAD model
    [front-silk.dxf, motor-board.FCStd]
2020-07-30 Modify motor encoder disk template
2020-07-31 Motor encoder disks: manual attempt, then PCB version
    [encoder-disk-outline.dxf, motor-board.kicad_pcb, motor-encoder-disk-outline.FCStd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]
2020-08-04 Starting on code: STM32F767ZI Nucleo BSP and test blinkies
    [motor-encoder-disk-B_Mask.gbr, motor-encoder-disk-B_Paste.gbr, motor-encoder-disk-B_SilkS.gbr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]
2020-08-10 Basic RX handling: interrupt, buffer, line handling
2020-08-11 First go at USART transmit DMA
2020-08-12 WIP: build tools; serial terminal using DMA TX
2020-09-27 Get PWM shell demo working
2020-10-26 Extend PWM code to support multiple channels
2020-10-26 Assembly helper
2020-10-26 Start motor driver TDD
2020-10-26 First round of motor driver TDD
2020-11-26 WIP: Waveforms setup for motor board testing; motor torque code
2020-11-27 Motor torque TDD; hardware mocking improvements
2020-11-27 Motor torque TDD: data collection
2020-11-29 Motor encoder TDD
2020-11-30 Rough speed calculations in motor encoder
2020-11-30 Motor controller TDD
2020-12-02 Motor shell application
2020-12-06 WIP: motor PWM working in shell-motor app
2020-12-06 WIP: motor torque data collection working
2020-12-06 WIP: motor encoder working in shell-motor app
